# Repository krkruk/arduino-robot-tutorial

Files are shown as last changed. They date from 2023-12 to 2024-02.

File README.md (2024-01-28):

# arduino-robot-tutorial

The following pages introduce you into a world of embedded programming in AVR-based
[Arduino platform](https://www.arduino.cc/).

This repository is organized into the following directories:

* [Tutorial - rendered page](https://krkruk.github.io/arduino-robot-tutorial/) or [`docs`](docs/README.md) if you prefer to read raw Markdown files. The core tutorial you need.
* `/docs/chapters/assets/code` and `mini-robot` - these directories contains all intermediate code samples as well as the final code that can be simply uploaded to your Arduino microcontroller given you follow all the suggestions presented in the tutorial
* `3d_models` - all necessary STL files (including Solid Edge Community editable versions) to print your own robot!

The tutorial assumes you are at least familiar with C-lang-like language. It is not meant
to teach anyone how to code in AVR/Arduino from scratch. It's more like a getting started
for anyone who has some experience at coding.

Remember, education is important. Consider signing up for a university course. I'm just
a random guy in the Internet ;). Don't trust in anything you read... The tutorial likely has some issues with it, sometimes it may be misleading etc. Common sense is your friend, Google (or any search engine) is your bestie.

## Disclaimer

All presented materials serve educational purposes only. Working with electricity
poses hazard to your health and life. If you decide to follow the tutorial,
you do it at your own risk. You can get destroy your electronic components (i.e., ESD - electrostatic discharge), get electrocuted, burn down your surroundings. You have been warned!

Similarly, 3D printing comes with it's own risks. My first cheap 3D printer caught fire twice...
You need some basic skills to operate FDM/FFF printer. Please refer to your printer user
manual. Remember, you do it at your risk!

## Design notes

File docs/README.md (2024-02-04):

# Tutorial overview

## Introduction

Have you ever dreamed of making your own electronic device? 
Do you think it's a difficult task and requires at least a PhD in electronics?
Well, we no longer live in *Stone Age* and there is no need to chisel transistors out of a silicon wafer. There are way better solutions on the market nowadays.

This tutorial presents an affordable way to your very first robotics. For ~€20-25 you can build your own robot that actually can fight! 

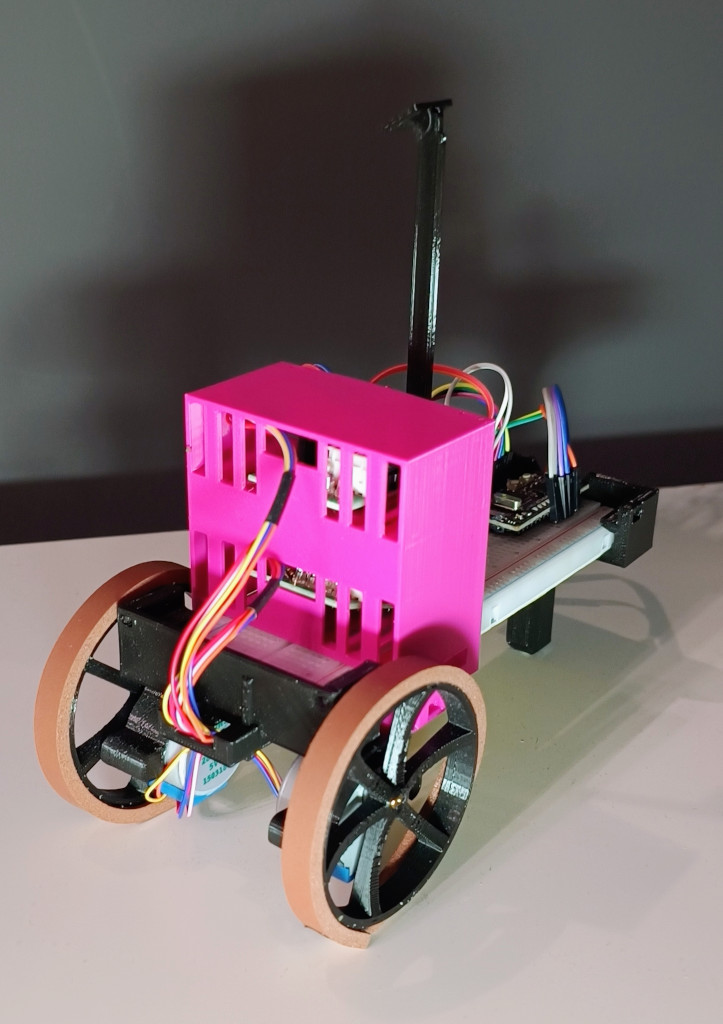
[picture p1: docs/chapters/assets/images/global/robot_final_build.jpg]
Robot - picture

<br />Figure: Completed robot, photo

> [!IMPORTANT]
> This tutorial assumes you have basic familiarity with one of C-like languages: C, C++, Java, JavaScript, Python.

This tutorial shall follow DRY principle: Don't Repeat Yourself. If there's a good resource, I'll simply point you there.

## Table of contents 
* [Hello World](chapters/0_hello_world.md)
  * Never seen an IDE? Want to test your set up? Come here!
* [I/O handling](chapters/1_io_handling.md)
  *  How to control pins in your board? Start here!
* [Analog input, Pulse Width Modulation](chapters/2_analog_and_pwm.md)
  * Life in between 0V and 5V
* [UART](chapters/3_uart.md)
  * Data transfer between PC and microcontroller
* [Controlling Stepper Motors](chapters/4_stepper_motor.md)
  * *You spin me right round round round...*
  * Full Step, Half Step, Arduino libraries
* [Controlling Servos](chapters/5_servo.md)
  * Torque and angle with a servo
* [Integrating knowledge - Building a robot!](chapters/6_robot_integration.md)
  * You are familiar with the basics by now. It's time to make a robot!

Your best friend during the course - [Atmega328P Datasheet](https://ww1.microchip.com/downloads/en/DeviceDoc/Atmel-7810-Automotive-Microcontrollers-ATmega328P_Datasheet.pdf)!

## Bill of materials

To complete the tutorial, you'll need:

* 1x justPi 830 breadboard (or other with compatible dimension)
* 1x Cytron Nano board (Arduino Nano board is a good choice too, though provides fewer features)
* 2x 28BYJ-48 stepper motors with ULN2003 driver (Darlington amp)
* 1x SG-92R servo (or similar)
* 1x set of jumper leads
* 1x set of resistors
* 1x set of LEDs
* 1x photoresistor 
* 1x microUSB cable
* 1x push button (optionally)
* 1x set of 3D printed elements (see below)

> [!NOTE]
> If you just want to learn basics you can complete the introductory chapters with only
> one stepper motor. You also don't need to 3d-print anything in that case!

## Bill of Materials: 3D printed elements
To complete the tutorial and build a robot, you'll need:

* 1x chassis_front_beam.stl 
* 1x chassis_rear_beam_with_airsoft_bearing.stl 
* 1x front_wall.stl  
* 1x rear_wall.stl 
* 2x stepper_motor_case.stl 
* 2x wheel.stl
* 1x driver_tower_with_servo.stl
* 1x servo_arm.stl
* 1x servo_arm_effector.stl
* 1x servo_holder.stl

Additionally:
* 1x plastic 6mm airsoft BB
  * That's your bearing and a part of the rear axle
* rubber strips to form a tyre (adhesive required). I used a window gasket/seal for this purpose. 
You can also cut a piece of a bicycle inner tube (so called *ranger band*). It fits perfectly and does
not require adhesives.
* Glue
* Some basic tools
* electrical tape
* a few zip ties can be quite handy too. Alternatively, you can use ancient technique of 
[cable lacing](https://en.wikipedia.org/wiki/Cable_lacing). After all, it's a formal NASA [NASA-STD-8739.4](https://s3vi.ndc.nasa.gov/ssri-kb/static/resources/nasa-std-8739.4a.pdf) standard.
Take a look at [NASA's website](https://workmanship.nasa.gov/lib/insp/2%20books/links/sections/401%20General%20Requirements.html).

All STL files can be downloaded from this tutorial repository: [3d_models](https://github.com/krkruk/arduino-robot-tutorial/tree/master/3d_models). 

The robot has been design to require no screws, bolts, anything. It's ugly but functional :).
Printing instruction:

* PLA is good enough. Some elements require precision of ~0.1mm 
* 6-10% fill
* 2 line wall thickness

Once you print all the parts, you'll have a robot that resembles the render photos below:

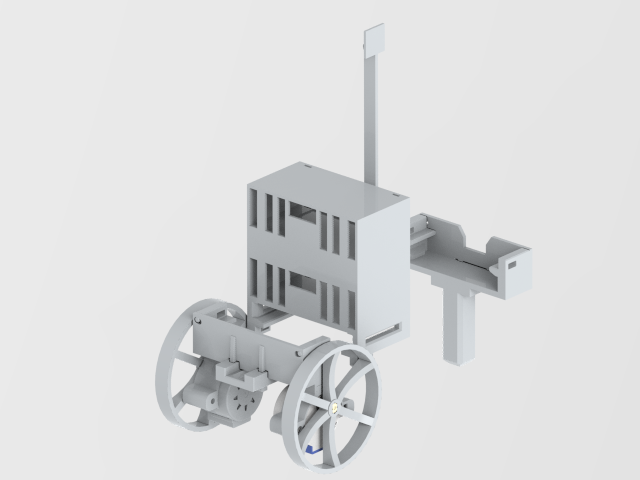
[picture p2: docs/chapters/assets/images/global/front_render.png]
Front render

<br />Figure: Front render

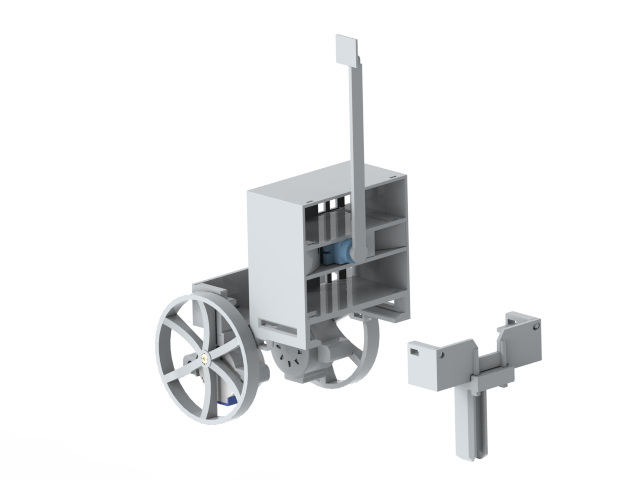
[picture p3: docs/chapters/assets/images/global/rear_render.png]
Rear render

<br />Figure: Rear render

## Integrated development environment

You need to install an integrated development environment to start developing your programs ASAP. It's the easiest and fastest way (of course you can use a standalone AVR Toolchain[^1] and AVRDude [^2]... it's your choice but make sure you have plenty of time and tenacity).

Since it's a quick way to get you started I suggest you install both, yes both, environments:

* VSCode/VSCodium + PlatformIO plugin. This is how you can do it: 
[Installation tutorial](https://docs.platformio.org/en/latest/integration/ide/vscode.html#ide-vscode)
* Arduino IDE - [download page here](https://www.arduino.cc/en/software)

Why two IDEs? Well, Arduino IDE is so simple that it's a very nice place to start. Lots of 
pre-installed examples that you can simply run. All toolchains install automatically (AVR, ARM, etc.). 
It provides an easy to use terminal to see UART data (refer to [UART](chapters/3_uart.md)). However, 
anything bigger than one file tends to be more and more difficult to maintain. 

VSCode is an advanced text editor that can work quite nicely as an IDE if you configure it properly. 
*PlatformIO* provides support for most of development boards available on the market. It also handles 
external dependencies quite well, so you don't need to download 3rd party libraries on your own. It 
all comes with a greater complexity and is slightly more difficult to use. Just slightly.

Now, sometimes it's easier to compile software in Arduino IDE than in VSCode. You download a lib, 
compile, and run. VSCode can sometimes be a pain in this aspect. So Arduino IDE is also a good tool 
for any quick debugging you may need.

## TL;DR; Skip tutorial, give me a robot

If you are impatient and want the robot now without following the tutorial,
here are all the steps you need to create your robot.

* 3d-print all elements you find in [`3d_models`](https://github.com/krkruk/arduino-robot-tutorial/tree/master/3d_models) directory. Use \*.stl files. Then, follow the assemble instructions
as provided in [Integrating knowledge - Building a robot!](chapters/6_robot_integration.md) chapter.
  in your favorite slicer software
* Follow the pinout as shown in the table
* Install the software on your Cytron board. Use README file distributed alongside
  the source code. Final code can be found [here](https://github.com/krkruk/arduino-robot-tutorial/tree/master/mini-robot/final_source_code).

**PINOUT**

| Device | Arduino Pin |
| --- | --- |
| Servo PWM line | D9 |
| Right Stepper IN1 | D7 |
| Right Stepper IN2 | D6 |
| Right Stepper IN3 | D5 |
| Right Stepper IN4 | D4 |
| Left Stepper IN1  | PIN_A4 |
| Left Stepper IN2  | PIN_A3 |
| Left Stepper IN3  | PIN_A2 |
| Left Stepper IN4  | PIN_A1 |

## Disclaimer

All presented materials serve educational purposes only. Working with electricity
poses hazard to your health and life. If you decide to follow the tutorial,
you do it at your own risk. You can get destroy your electronic components (i.e., ESD - electrostatic discharge), get electrocuted, burn down your surroundings. You have been warned!

Similarly, 3D printing comes with it's own risks. My first cheap 3D printer caught fire twice...
You need some basic skills to operate FDM/FFF printer. Please refer to your printer user
manual. Remember, you do it at your risk!

### References

[^1]: [GCC AVR Toolchain](https://www.microchip.com/en-us/tools-resources/develop/microchip-studio/gcc-compilers)
[^2]: [AVRDude](https://github.com/avrdudes/avrdude)

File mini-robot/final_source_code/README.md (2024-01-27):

# Arduino Robot Tutorial - Final Source code
## dependencies

* ArduinoJson 7.0.2 by Benoit Balnchon
* AccelStepper 1.64 by Mike McCauley
* arduino-timer 3.0.1 by Michael Contreras
* Stepper 1.1.3 by Arduino

## pinout

| Device | Arduino Pin |
| --- | --- |
| Servo PWM line | D9 |
| Right Stepper IN1 | D7 |
| Right Stepper IN2 | D6 |
| Right Stepper IN3 | D5 |
| Right Stepper IN4 | D4 |
| Left Stepper IN1  | PIN_A4 |
| Left Stepper IN2  | PIN_A3 |
| Left Stepper IN3  | PIN_A2 |
| Left Stepper IN4  | PIN_A1 |

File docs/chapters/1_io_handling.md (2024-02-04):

# Input/Output handling

**Contents**
* toc
{:toc}
Hopefully, you own an Arduino Nano-compatible board, just like the Cytron's one
mentioned in the *Bill of materials* page:

[Cytron Maker Nano pinout](https://www.cytron.io/p-maker-nano-simplifying-arduino-for-projects)

> [!IMPORTANT] 
> I strongly encourage you to support the original Arduino Project and the idea behind it! 
> Arduino enables thousands of people to develop hardware by reducing the learning curve.
> I strongly encourage you to buy one yourself!

The project can be completed using a standard Arduino Nano board.
The Cytron's board adds new features such as LEDs in all GPIO, a programmable button, and a buzzer. 
It's a nice touch if you want to reduce wiring in your final project.

> [!NOTE] 
> The board uses CH340C as a UART-USB converter. It's may not be compatible with your 
> operating system out of the box. 
> In *Ubuntu 22.04.3 LTS*, you'll need to configure it by uninstalling a package from your 
> system (it disables braille display): `sudo apt remove brltty` [^1]. MS Windows may require similar steps.

The Cytron's board uses Atmega328P as it's main microcontroller in the TQFP package. 
Luckily, you don't need to follow PCB paths to determine which board pin correspond 
to which IC pin. The pinout diagram above does it perfectly for you! Still, if it happens 
one day you need create your own PCB, it's worth to know physical 
dimensions and properties of your microcontroller (i.e. packaging, 
[DIP package](https://en.wikipedia.org/wiki/Dual_in-line_package)
or some sort of [SMD](https://en.wikipedia.org/wiki/Surface-mount_technology) like TQFP). 
You also want make yourself familiar with the original datasheet: 
[Atmega328P Datasheet](https://ww1.microchip.com/downloads/en/DeviceDoc/Atmel-7810-Automotive-Microcontrollers-ATmega328P_Datasheet.pdf). 
The datasheet provides all necessary information you need to start coding your microcontroller 
and tech specs that you should follow.

## PORTs, PINs and power output

What is a port, then? Well, in a realm of microcontroller, a port is a module that 
captures a signal from the real word, encodes and sends it over a data bus to CPU
([Processor, Central Processing Unit](https://en.wikipedia.org/wiki/Processor_(computing))) 
and/or other microcontroller peripheral elements.
A pin is a physical connector (a lead) that one can, for instance, solder onto a PCB. 
Pins are the true interface that the IC uses to interact with the world.

Atmega328p has 3 ports (PORTB, PORTC, PORTD) with built-in pull-up resistors. The 
microcontroller can therefore support up to 23 input/output pins 
(PORTC exposes 7 pins, the rest supports 8 pins). To visualize the overall Atmega architecture,
please refer to the documentation (chapter: 2). The block diagram (extracted from the datasheet *Chapter 2.1 Block diagram*):

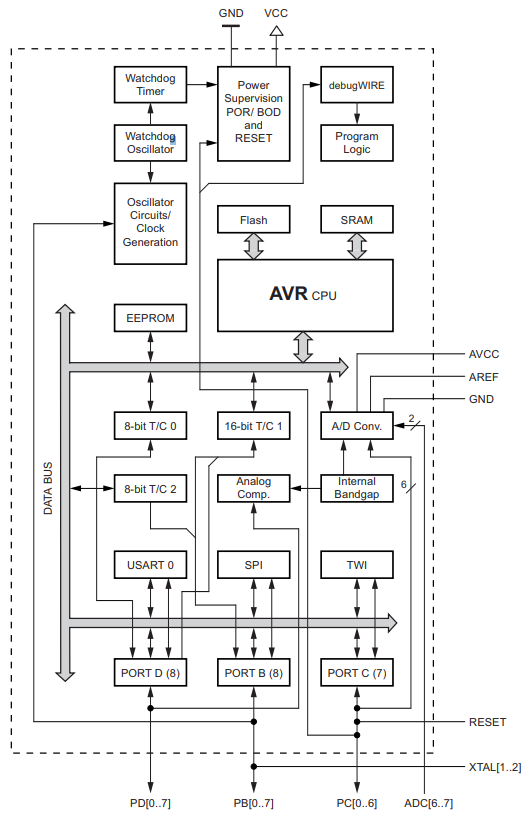
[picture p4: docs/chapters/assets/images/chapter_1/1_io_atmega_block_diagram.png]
Source: Atmega 328p datasheet, Chapter 2.1 Block diagram


That's a theory. You are not soldering your own PCB, you bought an off-the-shelf one. It means, 
you don't need to map pins defined in Atmega datasheet to your board outputs. Your Cytron's Nano is 
compatible with the original Arduino Nano, therefore you can re-use all resources known in 
Arduino to your advantage. Compare Cytron's pinout (the very first image in this page) with the 
table and the Arduino pinout below.

| PORT | Ardunio Nano | Cytron Maker Nano | Atmega328P |
|---|---|---|---|
| DDRB | D8 | D8 | PB0 |
| DDRB | D9 | D9 | PB1 |
| DDRB | D10 | D10 | PB2 |
| DDRB | D11 | D11 | PB3 |
| DDRB | D12 | D12 | PB4 |
| DDRB | D13 | D13 | PB5 |

[Arduino Nano Pinout](https://www.electronicshub.org/arduino-nano-pinout/)

`D\d` (for instance: `D8`, `D13`) is an alias for a given pin Arduino ecosystem. You don't need to
memorize anything. Your board has all the markings printed on the PCB solder mask itself. 
You will use the very same aliases such as `D8`, `D13` in your code if you decide to 
use Arduino framework. 
The Atmega328P pin aliases found in Atmega toolchain and are simply a shorthand for 
underlying pin addresses (i.e., `0x00`). You definitely want to use these aliases!
It improves overall readability and keeps your sanity intact anytime you decide to debug your code 
in future :).

If you want to know more about Nano board, you can refer to this page [^2].

## Digital output

> [!IMPORTANT] 
> Atmega328p pins are limited to 20mA (milli amps) per pin and up to 100/150mA for 
> a port. You should not connect anything more amp-consuming to a pin directly. Use a transistor 
> to amplify digital signals to an output that can handle bigger loads. You can read more on 
> amplifiers in [Wiki](https://en.wikipedia.org/wiki/Category:Single-stage_transistor_amplifiers). 
> Please, see also *28. Electrical Characteristics* in your Atmega datasheet [^3].

One more thing, Arduino Nano works in 5V logic. It means the high state (also referred as *1*) is 
5V and the low state is 0V (you guessed it! It's referred as *0*). That's the ideal condition, of course.
In the real world, *0* state can be considered as 1/3 VDD or lower of your voltage supply. 
Similarly, the high state is 2/3 VDD or higher [^4]. These are pretty good approximations.
You can also refer to *28.2 DC Characteristics* in datasheet for more details on 
input/out (high|low) voltages [^3].

Lots of theory, and no code so far. It's time to change it. Let's take a closer look to the 
blinking example we had in the previous chapter:

```
// Source: https://github.com/arduino/arduino-examples/blob/main/examples/01.Basics/Blink/Blink.ino

void setup() {
  // initialize digital pin LED_BUILTIN as an output.
  pinMode(LED_BUILTIN, OUTPUT);
}

// the loop function runs over and over again forever
void loop() {
  digitalWrite(LED_BUILTIN, HIGH);  // turn the LED on (HIGH is the voltage level)
  delay(1000);                      // wait for a second
  digitalWrite(LED_BUILTIN, LOW);   // turn the LED off by making the voltage LOW
  delay(1000);                      // wait for a second
}
```

The `setup()` function initializes hardware. It includes setting up a desired state on a pin,
interrupts, serial devices, etc.. Effectively, anything you need to run your main application code should be placed within the `loop()`.

The `loop()` function is effectively anything you want to run indefinitely as your firmware. 
This involves all ALU operations you want to run with help of your peripherals such as I/O pins, UART etc.

In order to blink an LED you always need to configure your port by telling a direction of a given pin, 
whether it's input or output. Possible options: `OUTPUT`, `INPUT`, `INPUT_PULLUP`.

Once this is done, you can then either write or read a pin state, depending on your direction 
configuration. To do so, you can use `digitalWrite(<<pin alias>>, <<state>>)` function. 
*Pin alias* can be a `uint8_t` value or a label such as `LED_BUILTIN`. *State* can be 
either `LOW` or `HIGH`.

Let's connect your own LED... You need an LED and a resistor. You should never connect an LED to a DC output as you will likely fry it. 

Basic LED circuit

First of all, if you have some experience in electronics you must know that LED is directional.
It means it acts as conductor if connected with correct polarity. If you connect it the other way 
around it won't conduct (well... until it does, briefly :)). The term is reverse current and it 
can be a feature sometimes. As this no 101 tutorial in electrical components, 
I suggest to take a look at Wiki [^5]. If you are in rush, I recommend taking a look at 
[voltage-current chart](https://en.wikipedia.org/wiki/File:Forward_and_Reverse_Characteristics_for_diodes-en.svg)
to understand how different LEDs can be.

S<sub>1</sub> voltage supply is the Arduino. It gives you 5V. LED requires 0.7V and 0.2mA to
light up. Now, you need to calculate what resistor is needed. 
The formula uses [Ohm's Law](https://en.wikipedia.org/wiki/Ohm%27s_law) and some 
[principles on connecting circuits](https://en.wikipedia.org/wiki/Kirchhoff%27s_circuit_laws) 
in series. I transformed it so it corresponds to the circuit

$$ R_1 = \frac{S_1 - D_1}{I} = \frac{5V - 0.7V}{20 \cdot 10^{-3}A} = 215 \frac{V}{A} = 215\Omega $$

Isn't the physics of electrics amazing? Now, you need to pick a resistor that matches the 
calculations. If you apply lower resistance value, you may fry your LED. I suggest to pick 220Ohm
resistor or higher. It's all math and diagrams. How to connect it? Well, let's go back to 
the real world. An LED has two leads: a short one and a longer one. The longer one is the 
'<strong>+</strong>' (katode) and the shorter one is '<strong>-</strong>' (anode). 
You want to connect your polarities in series, ie: `V+ - +R- - +D- - -V`. 
A '-' in component is a plus for the other one. You can also take a look at Adafruit's tutorial 
for more details [^6]. Oh, and as an interesting fact - the 
[colors on your resistor](https://en.wikipedia.org/wiki/Electronic_color_code) packaging matter!.

Please, construct your circuit as proposed here. You can use your jumper cables if you want:
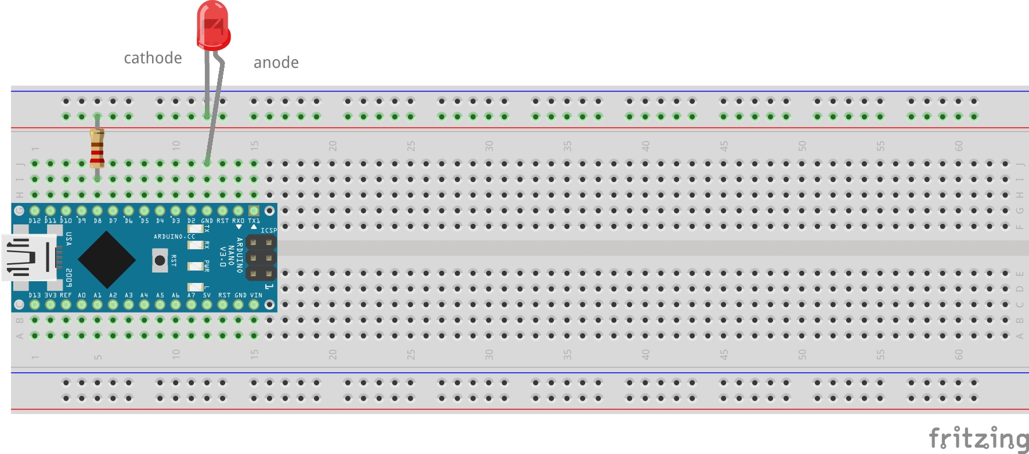
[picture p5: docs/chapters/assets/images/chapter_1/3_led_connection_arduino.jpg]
Arduino circuit

<br />Figure: Connecting an LED with a resistor

Now, the coding part! It's not that complicated
(source: [Incremental blink](./assets/code/chapter_1/1_incremental_blink/1_incremental_blink.ino)):

```
static constexpr const uint8_t HARDWARE_LED = 8;
static constexpr const uint8_t DELAY_RATE = 100;
static constexpr const uint16_t MAX_DELAY = 3000;

static uint8_t hardwareLedState = HIGH;
static uint8_t hardwareLedDelayCounter = 1;

void setup() {
  pinMode(HARDWARE_LED, OUTPUT);
  digitalWrite(HARDWARE_LED, HIGH); 
}

void loop() {
  uint16_t delayValue = DELAY_RATE * hardwareLedDelayCounter;
  ++hardwareLedDelayCounter;
  if (delayValue > MAX_DELAY) {
    delayValue = DELAY_RATE;
    hardwareLedDelayCounter = 1;
    hardwareLedState = HIGH;
  }

  hardwareLedState ^= 1;
  digitalWrite(HARDWARE_LED, hardwareLedState); 
  delay(delayValue);
}
```

The code increases delay time in each consecutive led state, i.e, 200ms - LOW, 
300ms - HIGH and so on. Note a new constant `HARDWARE_LED` - it matches `D8` pin in 
the Fritzing diagram above. If you use Cytron's board, you'll hear beeping sound too as `D8` pin
is connected to a buzzer

Ok, so how does it look like in pure AVR then. Well, in AVR context `setup()` and `loop()` functions
translate to this form:

```
int main() {
  setup();
  while(1) {
    loop();
  }
}
```

What Arduino Framework does is really it provides a layer of abstraction over the AVR microcontroller. 
It's way more developer friendly than dealing with raw registers. Speaking of registers, 
do you remember the blink example? This is pure AVR code 
(source: [AVR Blink](./assets/code/chapter_1/2_avr_blink/2_avr_blink.ino)):

```
#include <avr/io.h>
#include <avr/delay.h>

// This is the same hardware LED we introduced earlier!
#define HW_LED (1 << PB0)

int main() {

  /* setup() */
  DDRB = (1 << PB0);
  PORTB = (1 << PB0);  // light up the LED
  /* end: setup() */

  /* loop() */
  while (1) {
    PORTB ^= (1 << PB0);
    _delay_ms(1000);
  }
  /* end: loop() */
}
```

Isn't it way more complex, is it? Lots of bit shifts and poor readability. 
You certainly can see `setup()` and `loop()` blocks.

To initialize pin mode (remember: `pinMode()` function?), you need to follow documentation 
*13.2.3 Switching Between Input and Output* [^3] and set DDRB's value to 1, 
or precisely `0b0000 0001`. 
The port shall work as the output device allowing you to set/unset state. 
If you want to connect an LED to `D12` (also known as PB4), you can enable direction 
by assigning `DDRB = (1 << PB4)` or even `DDRB = 0b0001000`. 
To enable pin, you need to operate on a different register: `PORTB`. Operation `^=` means toggling a 
value under the given bit location. In Arduino, you would need to call 
`digitalWrite(pin, LOW|HIGH)` twice.

Clearly, AVR can be much harder to comprehend. So why bother? Well, some day you may be asked to 
implement a simple firmware on ATtiny13 (or similar), a microcontroller with very little resources. 
The AVR example requires 166 bytes, the Arduino one: 924bytes. Any framework shall add additional 
overhead and consume more flash disk space on your device. 
You need to be very conscious about resources and the platform limits 
(i.e., stack depth - nesting functions calls may also lead to errors!).

## Digital input and pull-up resistors
It's time to get some input events from the world. An obvious choice is a push button. 
A simple device that breaks a circuit if anyone pushes it...

Now, we already know that turning on an LED is to provide state **1**, which translates to 
5V potential at a pin. Good! How about we reverse the order. It'll be you who changes a potential 
on Arduino lead, which translates to a different state on a pin. All you need to do is to verify 
the state in the code!

Some theory is needed. You need to provide stable voltage on your pin. Otherwise, you can read 
any state state between 0 and 1, it'll float. This is why you need to construct a special circuit 
to support a button with a pullup resistor, such as this one:

Button circuit with pullup resistor

You are not limited to such a simple design. You can of course connect your button through a 
transitor, i.e., common collector circuit and/or a capacitor to the circuit to eliminate contact 
bounce [^7]. Eliminating contact bouncing can be done 
[programmatically](https://docs.arduino.cc/built-in-examples/digital/Debounce) but it's a rather tedious job to do.

More on pullup resistors can be found on Sparkfun's learning portal [^8] and debouncing here [^9].

Ok, that's all for now. It's a 3h tutorial after all. Let's do some coding. The Cytron board you 
have already has a push button! Let's use it! This is the button schematics (retrieved from 
Cytron's docs):

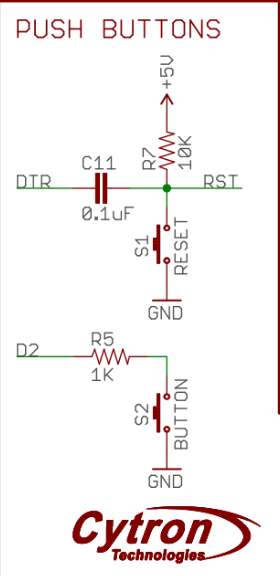
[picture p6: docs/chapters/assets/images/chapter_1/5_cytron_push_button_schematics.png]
Cytron Nano board - push button schematics
.

We are interested in the bottom part of the diagram. We can use programmatically `D2` pin. I hope 
you spotted that the button does not support physical debouncing, unfortunately. You can either 
code it on your own, based on the given resources or simply dismiss it. Here's a simple code 
snippet that changes an LED state anytime you press the button and keeps it until you push the 
button again (source - [3_pullup_and_software_debouncing](./assets/code/chapter_1/3_pullup_and_software_debouncing/3_pullup_and_software_debouncing.ino)):

```
static constexpr const uint8_t PUSH_BUTTON = 2;
static uint8_t builtinLedState = LOW;

void setup() {
  pinMode(LED_BUILTIN, OUTPUT);
  pinMode(PUSH_BUTTON, INPUT_PULLUP);
  digitalWrite(LED_BUILTIN, builtinLedState);
}

void loop() {
  uint8_t pushButtonState = digitalRead(PUSH_BUTTON);
  if (pushButtonState == LOW) {
    delay(50);                                    // simple programmatic debouncing
                                                  // You should measure the precise debouncing period
                                                  // with an oscilloscope. 50ms is just an educated guess
    pushButtonState = digitalRead(PUSH_BUTTON);

    if (pushButtonState == LOW) {
      builtinLedState ^= 1;                       // toggling the LED state
      digitalWrite(LED_BUILTIN, builtinLedState);

      while (digitalRead(PUSH_BUTTON) == LOW);    // blocking the program until
                                                  // the user releases the button
    }
  }
}
```

Interesting code parts: `pinMode(<<pin>>, INPUT_PULLUP|INPUT)`.
This is a pullup configuration for `D2 button`. From now on, you can read the state on 
the `D2` pin!. `digitalRead(<<pin>>)` function reads the state, either `HIGH` or `LOW`.

Another, *weird* part of the code is the nested if-statement and a delay function. Well, this is 
software debouncing. You push the button and connectors start to bounce back and forth. The 
program waits another 50ms until the connectors stabilize. The state should no longer float on 
that pin by the time the program reads the state again. If it is indeed low again, you change the
state of the button.

Note the last `while` loop at the end of the snippet. It blocks the application until 
the user releases the button. This is to prevent instant state toggling of the LED. 
Comment this out and see how your board behaves!

Now, how can you code the same thing in AVR? Let's see 
(source: [4_pullup_and_software_debouncing_avr](./assets/code/chapter_1/4_pullup_and_software_debouncing_avr/4_pullup_and_software_debouncing_avr.ino)):

```
#define LED_BUILTIN (1 << PB5)
#define PUSH_BUTTON (1 << PD2)

int main() {

  // setup()
  DDRB = LED_BUILTIN;
  DDRD = 0x00;          //set the enitre port as input - including PD2

  PORTB = 0x00;
  PORTD = PUSH_BUTTON;  //PD2 is set as input and the state as HIGH - pullup enabled

  // loop()
  while (true) {

    // the push button is pressed if it's state is 0

      if (bit_is_clear(PIND, PD2)) {  // much clearer than: !(PIND & (1<<PD2))
        _delay_ms(50);
        if (!(PIND & PUSH_BUTTON)) {
          PORTB ^= LED_BUILTIN;
          while (bit_is_clear(PIND, PD2));
        }
      }
  }
}
```

There are some major differences between this code and the Arduino one.
First of all, the state is kept in registers rather than in an application stack. 
There is also an additional register 
used: `PIND` (see docs: *13.4.10 PIND* [^3]). The register is responsible for reading the state 
on Atmega's lead. It returns all 8 bytes, each byte corresponds to one of the pins in your board. 
To read the state on PD2, you need to run some shifts to get data. Let's decipher this bit, 
assuming you actually keep holding the button:

```
values for:
  PIND = 0b???? ?0?? = 8 (? means state unknown)
  PD2 = 2
  1<<PD2 = 0b0000 0100 = 4

// button is pressed, state on the button lead is 0
1. !(PIND & (1<<PD2))
2. PIND & (1<<PD2)  --> 0b?????0?? & 0b00000100 = 0b00000000 = 0
3. !(0b00000000) = !(0) = !(false) = true  // zero is considered as false in C/C++/python
4. result: true

// button is released, state on the button lead is 1
  PIND = 0b???? ?1?? = 8 (? means state unknown)

1. !(PIND & (1<<PD2))
2. PIND & (1<<PD2)  --> 0b?????1?? & 0b00000100 = 0b00000100 = 8
3. !(0b00000100) = !(8) = !(true) = false // any non-zero number in C/C++/python is always considered as true
4. result: false
```

So really, all this complex math on bytes is all about reading a state on a given lead. If you
decide to use Arduino library, it's way easier to do so! Of course, it all comes with a price.
This is hex size for each framework:
* AVR hex size: 184 bytes
* Arduino hex size: 1086 bytes, more than 1kiB!

Good job! You know how to blink your LEDs both programmatically and with a push button. That's 
quite a lot. Really, interacting with a microcontroller is all about sending and receiving ones 
and zeros. All subsequent chapters only extend that notion! Can you imagine manually pushing and 
releasing a button 1000 times a second? This is what you will learn in the PWM chapter. Well, 
you'll learn how to do it programmatically, at least ;)

Let's move on to the next topic: interrupts. It's not the best idea to run blocking operations 
in the main program loop after all.

## Interrupts

Last but not least, we shall take a look at interrupts in this section. What is an interrupt? Well,
it's a mechanism that allows reacting to external (or internal) events outside of the main 
program loop? Wait, what? Let's take a look at an example, this time it'll be AVR code first 
(source - [5_interrupts_avr_toggle_led](./assets/code/chapter_1/5_interrupts_avr_toggle_led/5_interrupts_avr_toggle_led.ino)):

```
#include <avr/io.h>
#include <avr/interrupt.h>
#define LED_BUILTIN (1 << PB5)
#define PUSH_BUTTON (1 << PD2)

ISR(INT0_vect) {                   // magic here: Interrupt Service Routine
  PORTB ^= LED_BUILTIN;
}

static void setup() {
  DDRB = LED_BUILTIN;
  DDRD &= !(PUSH_BUTTON);          // pin as input
  PORTD = PUSH_BUTTON;             // pull-up

  EIMSK = 1 << INT0;               // enable PD2/INT0 as an interrupt source
  EICRA = 1 << ISC01;              // Enable direction of interrupt on INT0, 
                                   // falling edge
}

int main() {
  setup();
  sei();                           // enable global interrupts, SREG register

  while (true) {
    // idle, do nothing
    _delay_ms(10000);
  }
}
```

If you take a closer look at `while (true)` loop, you see it does nothing but sleeping. A good 
nap is nice but this is not why you bought your board to simply let it sleep... 
You want it to work for you and blink an LED!. If you compile it and start pressing 
the button you see that the LED turns on and off. Why? The interrupt!

There are some lines that can be somehow surprising. First of all `sei()` function. It enables 
global interrupts in `SREG` registry as documented in *6.3.1 SREG – AVR Status Register* [^3]. 
It's important not to forget to use it. In my personal experience, forgetting running this 
function is the most common reason why my interrupt routines don't work... it's because I don't 
enable them in the first place... There's also a function that has exactly opposite effect: 
`cli()` - it disables interrupts. It sometimes is handy as well.

Ok, interrupts are enabled. Now, we need to use PB5 (push button) pin as interrupt! 
Atmega328p offers two I/O pins as a source for external interrupts. 
Not much but still, we need to work with things we 
have\*. If you take a look at Arduino pinout from in the top of this page you'll notice that `PB5`
has also `INT0` label. That's the interrupt! Smartly design board, isn't it?

> \*you can set up interrupts as *PCIEx* that generates interrupts on many pins but it's out of 
scope of this tutorial

The setup functions sets up the `PB5` as a standard pullup-enabled input pin. There are two 
suspicious registers `EIMSK` and `EICRA`. `EIMSK` allows you to enable `INT0` as an interrupt 
source (vector) - see documentation *12.2.2 EIMSK – External Interrupt Mask Register* [^3]. The 
documentation states you need to set up an activation property to either raising or falling edge. 
You need the falling edge as you use a pullup-resistor. It means the high potential on the lead. 
So anytime you press the button, the potential goes to zero, hence the falling edge.
Of course, you can reverse that logic and use to your advantage. After all, it's all about
making engineering decisions.

Now, the most important part: `ISR()`. ISR is a special macro that handles interrupts in AVR. An 
*average* ISR body should be very concise and efficient. No long running operations as you block 
the main loop! Disabling interrupts and re-enabling them can be also a good idea if your code is 
highly asynchronous. You also should store `SREG` value to make sure you don't disable anything 
by mistake. ISR should then look more like this:

```
volatile uint8_t tmpSREG = 0;

ISR(INT0_vect) {                   // magic here: Interrupt Service Routine
  tmpSREG = SREG;
  cli();
  PORTB ^= LED_BUILTIN;
  SREG = tmpSREG;
}
```

Luckily, Atmega does this operation automatically, so you don't need to specify any `tmpSREG` 
variables [^10]. Hope, you noticed `volatile` keyword. Interrupts modify data outside of a 
regular program loop impacting the value that can be read from such a variable. The keyword 
prevents a compiler from optimizing the variable, improving stability of your application.

So what's an interrupt? A routine that reacts on an external/internal event and runs small 
portions of code called routines outside of a regular program loop. Hope, it's clear now. 
However, can you do the same thing in an easier way? Yes, you guessed it! Let's use Arduino this 
time! So here's the code that does the same thing, with no debouncing (source - 
[5_interrupts_avr_toggle_led](./assets/code/chapter_1/5_interrupts_avr_toggle_led/5_interrupts_avr_toggle_led.ino)):

```
static constexpr uint8_t PUSH_BUTTON = 2;
volatile uint8_t builtinLedState = LOW;

void toggleLed() {
  builtinLedState ^= 1;                       // toggling the LED state
  digitalWrite(LED_BUILTIN, builtinLedState);
}

void setup() {
  pinMode(LED_BUILTIN, OUTPUT);
  pinMode(PUSH_BUTTON, INPUT_PULLUP);
  digitalWrite(LED_BUILTIN, builtinLedState);
  attachInterrupt(                            // enabling interrupts on D2
    digitalPinToInterrupt(PUSH_BUTTON),       // mapping D2 to Atmega's INT0
                                              // this is for readability
    toggleLed,                                // a pointer to function, simply pass
                                              // a name of your function, it's not that scary!
    FALLING);                                 // activate the interrupt on falling edge
}

void loop() {
  delay(10000);
}
```

Hope, the resemblance is obvious... `toggleLed()` function simply performs a toggle operation on 
your built-in LED, using an external state variable. `enableInterrupt` well... enables the 
interrupt in nearly plain English. `digitalPinToInterrupt` maps a pin number to a corresponding 
event source pin, here `INT0`. This is certainly more readable and does not require much of 
knowledge on your board pinout. `toggleLed` here is simply passing a pointer to `toggleLed` 
function. You can use a more explicit way to show it's a pointer: `&toggleLed`, although I find 
it a bit of an overkill. Finally, you need to define a trigger that activates your interrupt. 
Choose FALLING trigger and keep in mind that there other options such as `LOW|CHANGE|RISING` [^11]. 

The `enableInterrupt` function works for digital pins only. Implementing a custom `ISR` can be 
more generic. Atmega328p support 26 input vectors as defined in 
`11.1 Interrupt Vectors in ATmega328P` [^3]. You can also browse `avr/iom328p.h` header to 
get the vector list:

```
[...]
/* Interrupt Vectors */
/* Interrupt Vector 0 is the reset vector. */

#define INT0_vect_num     1
#define INT0_vect         _VECTOR(1)   /* External Interrupt Request 0 */
// [...]
```

To summarize, the interrupts mechanism is a very handy tool if you want to support multiple 
actions in almost the same time. It allows you to act upon any external event 
and handle it efficiently.

Using interrupts and other Atmega peripherals allows you to implement a solution that appears to 
perform several actions in the same time. Multitasking, my friend :)!

## Analog input and output - ADC and PWM

Digital electronics, as your Atmega328p, is all about zeros and ones. 
There are no values in between, ideally. Thus, it's a rather hard task to talk about analog 
values in between 0-5V. Luckily, we are not exactly bound to 2 states only. We can change a pin 
state fast enough to reduce output power in a given timespan - this is called PWM, *Pulse
Width Modulation*. It's a rather important aspect of embedded programming, therefore
please read the next chapter that handles PWM in details.

There are also Arduino boards that support DAC - Digital-to-Analog converters, such
as [Arduino Due](https://store.arduino.cc/products/arduino-due). Unfortunately,
Atmega 328p microcontroller, as the one in your board, does not support DAC. For more details,
take a look at Wiki: 
[Digital-to-analog converter](https://en.wikipedia.org/wiki/Digital-to-analog_converter).

You can also read analog values with your microcontroller. Atmega328p comes with a 10-bit ADC and 
comparator built-in! ADC stands for Analog-Digital-Converter, which effectively translates voltage to 
a 10-bit value: 0-1023 integer value. More on ADC in the next chapter!

# References

[^1]: [CH340 Configuration in Ubuntu 22.04](https://askubuntu.com/questions/1403705/dev-ttyusb0-not-present-in-ubuntu-22-04)
[^2]: [Electronics Hub - Arduino Nano Pinout](https://www.electronicshub.org/arduino-nano-pinout/)
[^3]: [Atmega328P Datasheet](https://ww1.microchip.com/downloads/en/DeviceDoc/Atmel-7810-Automotive-Microcontrollers-ATmega328P_Datasheet.pdf)
[^4]: [Wiki - Logic Levels](https://en.wikipedia.org/wiki/Logic_level#Logic_voltage_levels)
[^5]: [Wiki - Diode](https://en.wikipedia.org/wiki/Diode)
[^6]: [Adafruit - Connecting LEDs](https://makecode.adafruit.com/learnsystem/pins-tutorial/devices/led-connections)
[^7]: [Wiki - Contact bounce](https://en.wikipedia.org/wiki/Switch#Contact_bounce)
[^8]: [Sparkfun - Pullup resistors](https://learn.sparkfun.com/tutorials/pull-up-resistors/all)
[^9]: [Physical Computing - Debouncing](https://makeabilitylab.github.io/physcomp/arduino/debouncing.html)
[^10]: [Stack Overflow - May I use cli() and sei() in the interrupt?](https://stackoverflow.com/questions/65112480/may-i-use-cli-and-sei-in-the-interrupt)
[^11]: [Arduino - attachInterrupt](https://www.arduino.cc/reference/en/language/functions/external-interrupts/attachinterrupt/)

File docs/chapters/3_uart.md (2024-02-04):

# Universal Asynchronous Receiver-Transmitter
**Contents**
* toc
{:toc}
So far, you've been blinking LEDs in one way or another. It's time to let your board talk to your PC too!.

See *19. USART0* chapter in Atmega328p Datasheet for very detailed UART tech specification [^1].

## Introduction

Serial port, [UART](https://en.wikipedia.org/wiki/Universal_asynchronous_receiver-transmitter) or 
[Universal Asynchronous Receiver-Transmitter](https://en.wikipedia.org/wiki/Universal_asynchronous_receiver-transmitter)
is a way that allows you to connect easily your device with PC and exchange data.

Asynchronous means that receiver/transmitter does not have to run at the same pace. Clocks of both 
devices can run at different frequencies or be out of phase. UART uses start and stop bits to 
determine when the transmission is over. This gives a great advantage. The protocol can work with no 
difficult clock synchronization techniques and technologies. 
Therefore, UART can be used at longer distances, speaking more of meters (yards) rather than 
centimeters (inches).

There are two industry wide standards of UART: [RS-232](https://en.wikipedia.org/wiki/RS-232) 
and [RS-485](https://en.wikipedia.org/wiki/RS-485). We are going to use a different route, though: TTL 
(Transistor-to-Transistor Logic) and connection via UART-USB bridge. In other words, you'll use Atmega 
integrated circuit, connect it to a 3rd party silicone chip (such as CH340, PL2303, FT232RL and many other) and plug a USB connector to your PC. You can even use another 
Atmega to host a USB (for instance Atmega16u4 with hardware USB support [^2])

Good news is your Arduino board (either Cytron's or the genuine one) comes with UART-USB converter. From coding perspective, you don't need to do anything.

A traditional UART tutorial presents and explains a data frame - a sequence of bits that form a single 
portion of a message... Let's get over with it now (image source: 
[Wiki - by Cody Hyman](https://pl.wikipedia.org/wiki/Plik:Serial_frame.png)):

UART data frame

Isn't it nice? Well, let me explain it from a perspective of typical parameters one typically uses:

* [baudrate](https://en.wikipedia.org/wiki/Baud) (popular: 9600, 115200) - originally, baud rate is a number of symbols/pulses emitted in a unit of time. In context of UART communication, think `baudrate=bitrate=bits per second` [^3]. Good enough, we are not purists here. And one more thing, the bigger the number, the faster is data transmission.
* dataframe (popular choice: 8 bits, 7-9 possible) - simply how many data bits shall be placed between the start bit and parity/end bits
* parity (set to no-parity) - a checksum bit, you can use it or simply ignore it. I prefer to ignore it. Other options are even and odd parity
* stop bits (popular choice: one; other options: one and a half, two bits)
* flow control (Arduino choice: No Flow Control) - UART supports two leads: RTS (Request to Send) and CTS (Clear to Send). Arduino uses TX and RX pins only, so there is no need to bother.

For a more detailed explanation, please refer to external sources such as this one: [UART - A hardware communication protocol](https://www.analog.com/en/analog-dialogue/articles/uart-a-hardware-communication-protocol.html) and other.

If you are going to connect your UART device to another device, make sure that:
* Baudrate must be the same for both a receiver and a transmitter
* Voltage levels are compatible: 5V-5V in both devices. Your device uses 5V as it's V<sub>cc</sub> voltage. If you connect to a device that uses 3.3V, you'll likely fry it. Hence, a [logic level converters/level shifter](https://en.wikipedia.org/wiki/Level_shifter) should be introduced.
* Cross your comm lines: `TX` (transmit line) should be connected to `RX` (receive line)
* NEVER FORGET ABOUT THE GROUND!!! GROUND IT!!! Actually, `GND` line should be the first line you connect and the first line you check if something is wrong. Seriously, you'll save lots of time by following this tip!

`TX1` pin is your transmitter and `RX0` is the receiver in your board. Take a look at it. Of course, you can simply use a USB cable if you plan to use PC comm only.

### Serial Monitors

You can use your serial device with a 3rd party tool or your custom software. If you decide to simply
browse or even plot data you can use some of these tools.

Windows:
  * [GUI] Arduino IDE - embedded serial monitor
  * [GUI] PlatformIO - embedded serial monitor
  * [GUI] [PuTTY](https://www.putty.org/)
  * [CLI] [Tabby](https://tabby.sh/)

Linux:
  * [GUI] Arduino IDE - embedded serial monitor
  * [GUI] PlatformIO - embedded serial monitor
  * [CLI] [minicom](https://en.wikipedia.org/wiki/Minicom)
  * [CLI] [Tabby](https://tabby.sh/)

If you are interested in writing your own software, you need a library or [follow a Lord's blessed path](https://en.wikipedia.org/wiki/TempleOS) and write your own library. It's up to you. Personally, I worked with the following:

* C++: 
  * Qt Framework, [Qt Serial Port](https://doc.qt.io/qt-6/qtserialport-index.html)
  * Boost Asio, [Serial Port](https://beta.boost.org/doc/libs/1_66_0/doc/html/boost_asio/reference/serial_port.html)
* python: [pyserial](https://pyserial.readthedocs.io/en/latest/pyserial.html)
* Java: [jSerialComm](https://fazecast.github.io/jSerialComm/)

## SerDes - Serialization and Deserialization

Data *serialization* is a process of converting data into a format that can be transmitted over 
wire/air and decoded at a destination point. The reverse process is called *deserialization*.

The keyword is **format**. You can choose two options: text or binary. The text option is usually 
human readable, supported by formats such as CSV, JSON, HTML, anything custom. The binary format 
converts data into a series of bytes, sometimes applying compression. You need to use the same 
serialization/deserialization technique in both receiver and transmitter to successfully deliver a 
message. Otherwise, the message can be consider as a series of random useless bytes.

Which one is better? Well, it depends. The binary format usually comes with big frameworks that can 
convert a *schema* into your C or C++ code. All you need to do is to compile a schema file and link 
generated files to your program. IMO, the greatest disadvantage of the binary format is difficulty to 
handle data packets. Since all your data is binary, you don't really know when the message stops and 
another message begins. A byte of binary data is really an 8-bit number, which translates to 0-255
(dec). Microcontroller is not aware of what the byte means. The binary formats of your choice usually 
provides libraries to capture a whole message and deserialize it, such as 
[protobuf](https://github.com/protocolbuffers/protobuf) or [msgpack](https://msgpack.org/), [ROS Messages](https://wiki.ros.org/Messages). 
Of course, you can implement something custom too - see the note below.

You can use text format too! It has several advantages: 1) it's human readable, 2) easy to find the 
last character, usually a new line character `\n`. Text format narrows down a range of values we send 
in a single byte from the binary data perspective. [ASCII](https://pl.wikipedia.org/wiki/ASCII) 
encodes human readable numbers as characters starting from a value 32 (in decimal, space `<<space>>`) 
up until 126 (dec, `~` character). Numbers between 0-31 and 127 
are special characters, such as *new line* character `\n` 10 (decimal). Thanks to this trick, a 
microcontroller can listen to a sender and cache raw bytes incoming from another UART device until it 
receives a byte of value 10 (dec, a new line character). You received a full line, a message that can be processed!

> [!NOTE]
> Long time ago, I was playing with robotics and European Rover Challenge. My team and I didn't know 
> anything about electronics and coding back then. We needed to control a robotic arm with 8 
> effectors. We developed a binary format -> one byte to control all 8 devices: `AAAV VVVV`. 
> `AAA` - 3 address bits, `VVVVV` - a value between 0-31. This technique allowed 
> us to control a 6-DOF arm without really any worries about a data package start and 
> stop positions. All we needed to do was to read just one byte to rule it all :)!

In my experience, hobby projects work very nicely with JSON (text) encoding. Simply, read a line of 
text data and deserialize JSON into individual variables. I recommend ArduinoJson[^4].

ArduinoJson deserialization example (source: [JsonParserExample](https://github.com/bblanchon/ArduinoJson/blob/7.x/examples/JsonParserExample/JsonParserExample.ino))

```
// ArduinoJson - https://arduinojson.org
// Copyright © 2014-2024, Benoit BLANCHON
// MIT License
//
// This example shows how to deserialize a JSON document with ArduinoJson.
//
// https://arduinojson.org/v7/example/parser/

#include <ArduinoJson.h>

void setup() {
  // Initialize serial port
  Serial.begin(9600);
  while (!Serial)
    continue;

  // Allocate the JSON document
  JsonDocument doc;

  // JSON input string.
  const char* json =
      "{\"sensor\":\"gps\",\"time\":1351824120,\"data\":[48.756080,2.302038]}";

  // Deserialize the JSON document
  DeserializationError error = deserializeJson(doc, json);

  // Test if parsing succeeds
  if (error) {
    Serial.print(F("deserializeJson() failed: "));
    Serial.println(error.f_str());
    return;
  }

  // Fetch the values
  //
  // Most of the time, you can rely on the implicit casts.
  // In other case, you can do doc["time"].as<long>();
  const char* sensor = doc["sensor"];
  long time = doc["time"];
  double latitude = doc["data"][0];
  double longitude = doc["data"][1];

  // Print the values
  Serial.println(sensor);
  Serial.println(time);
  Serial.println(latitude, 6);
  Serial.println(longitude, 6);
}

void loop() {
  // not used in this example
}
```

ArduinoJson will be used by default in subsequent chapters. Make sure to install it! Go to `Tools -> Manage Libraries...`, type `ArduinoJson` and click *Install*:

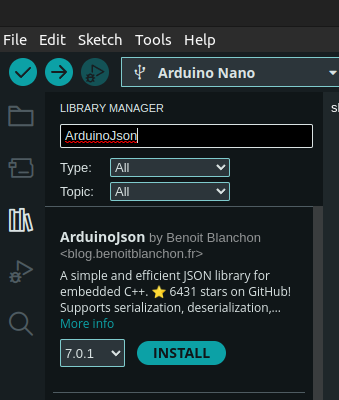
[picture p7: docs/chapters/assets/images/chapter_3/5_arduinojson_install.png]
ArduinoJson - Install steps


## Arduino Framework

Arduino allows using serial communication with ease. Make sure you familiarize yourself with documentation[^5].

### Serial initialization

This section shall present you how to write data to your PC. To connect with your microcontroller,
you can use Arduino Serial Monitor, PlatformIO Serial Monitor, minicom or really anything you
enjoy. The following examples shall use Ardunio Serial Monitor and minicom interchangeably.

Go to `Tools -> Serial Monitor`:

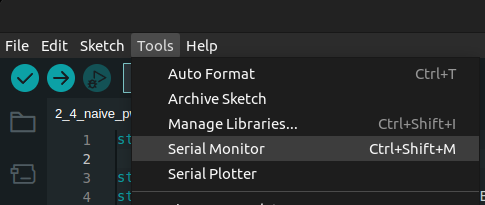
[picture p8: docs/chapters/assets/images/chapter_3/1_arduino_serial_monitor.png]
Arduino Serial Monitor


You'll see a new section at the bottom of your window. Make sure baudrate, newline setting and USB port are selected as shown in the picture (if you use Windows, port can be something like `COM7`):

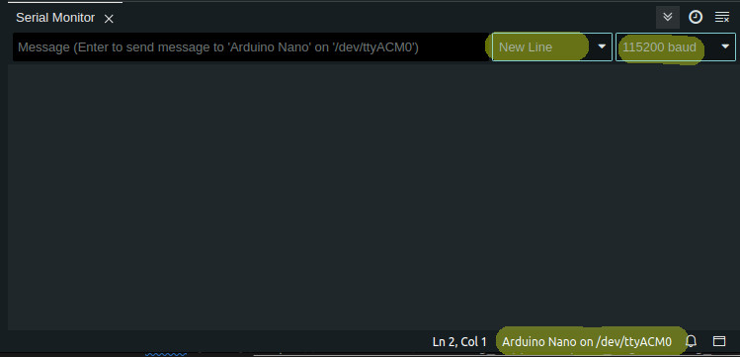
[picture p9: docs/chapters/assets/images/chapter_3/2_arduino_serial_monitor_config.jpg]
Arduino Serial Monitor - CLI


To start `minicom`, enter the following:

```
$ minicom -b 115200 -D /dev/ttyACM0
```

Minicom opens with `baudrate=115200`, 8-bits dataframe, 1 stop bit, no parity. Just like the Arduino Serial Monitor and the default Arduino Serial config (`SERIAL_8N1`)

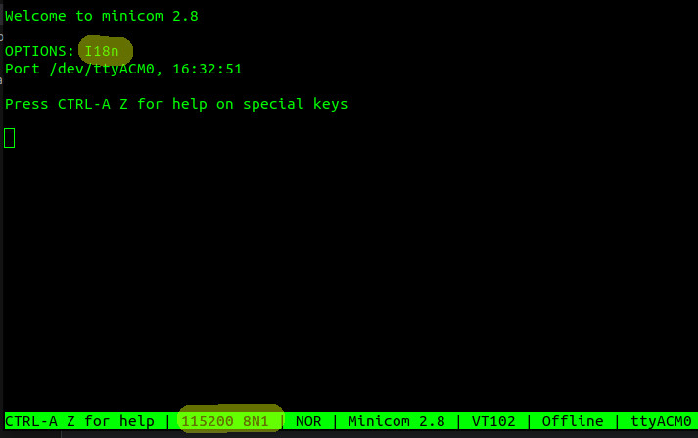
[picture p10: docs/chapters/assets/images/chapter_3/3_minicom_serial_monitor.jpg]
Minicom - Serial Monitor


You know how to open a serial monitor, now it's worth knowing how to start UART communication in Arduino.

There are two steps:

1. Initialize serial with baudrate and other config
1. Wait until a serial peripheral module starts (busy waiting)

Let's see some code (source - [Arduino Serial Initialize](./assets/code/chapter_3/arduino_serial_initialize/arduino_serial_initialize.ino)):

```
void setup() {
  Serial.begin(115200);
  while(!Serial) continue;
}

void loop() {
}
```

That's it! Isn't it simple? You probably have a feeling that these two lines hide some complex
register calls. That's correct! Let's now just focus on the positives: it takes two lines to enable Serial.

`Serial.begin(<<baudrate>>[, <<config, default: SERIAL_8N1>>])`[^6] initializes serial port to 
a given baudrate. Optionally, you can specify additional config for serial, should you need it. 
Otherwise, just enjoy simplicity of the API. Note that `Serial` is effectively a global variable 
that represents hardware serial. If you own an Arduino Mega, Due or any other that happened to support 
multiple UARTs, you can use other ports as well: `Serial1`, `Serial2`. You just need to make sure you 
connect necessary cables accordingly.

`while (!Serial) continue;` performs a busy waiting operation. The application waits here until the serial is initiated successfully. The implementation of `Serial` provides an overloaded `operator bool()`[^7]. 

Alright, we are ready to finally send some data to PC!

### Write data
#### Write a simple line

Without further edo, this is the code (source: [Arduino - UART Hello World](./assets/code/chapter_3/arduino_serial_hello_world/arduino_serial_hello_world.ino)):

```
void setup() {
  Serial.begin(115200);
  while(!Serial) continue;
}

void loop() {
  Serial.println("Hello World!");
  delay(1000);
}
```

To write a line, simply use `Serial.println()` function[^8]. It accepts raw strings 
such as `char *` and provides an overload for typical data types, such as `int`. 

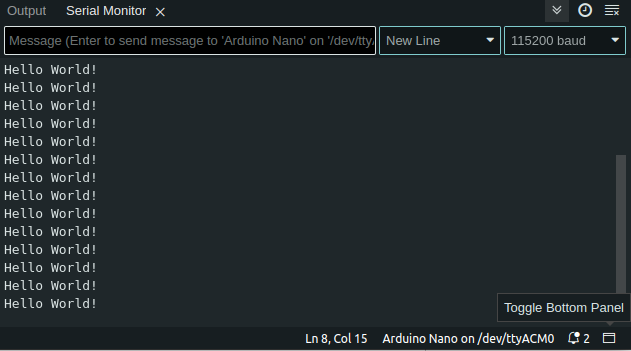
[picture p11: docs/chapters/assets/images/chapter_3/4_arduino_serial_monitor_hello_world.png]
Arduino Serial Monitor - Hello World


If you want to send an `int`, you can also
choose to print it either as decimal, octal or hexadecimal value, i.e.:

```
  Serial.println(15, DEC);
  Serial.println(15, BIN);
  Serial.println(15, OCT);
  Serial.println(15, HEX);

  result:
    15
    1111
    17
    F
```

Of course, there is also a function that does not add new line characters: `\r\n`. You can use [`Serial.print`](https://www.arduino.cc/reference/en/language/functions/communication/serial/print/).

Both `print()/println()` functions send data in a text format. Well, at least this is how data should
be interpreted at a receiving end. You can also send binary data with `Serial::write` function[^9]. As 
this course uses text-based serialization, I'll leave the binary part to study on your own. You can 
make it!

#### Write a line, substitute placeholders

Printing a static text is nice, but this is not how you use programs. You put data in and expect some results returned. How to send variable data? There are several options:
* Combine `print` and `println` into a sequence of calls
* Create a buffer string and generate a custom string
* Use a custom serializer: ArduinoJson or anything else
* Go with some sort of binary serialization and libraries

In this section, we'll try to go with the second approach (source - [Arduino - Buffer and sprintf](./assets/code/chapter_3/arduino_serial_buffer_sprintf/arduino_serial_buffer_sprintf.ino)):

```
#include <string.h>

static const constexpr uint8_t TXT_BUFFER_SIZE {64};
static char const TXT_BUFFER[TXT_BUFFER_SIZE] {'\0'};

static int counter {0};

static const char *HELLO_WORLD_LABELS[] = {
  "Hello World",
  "HELLO WORLD",
  "HeLlO WoRlD!"
};

void setup() {
  Serial.begin(115200);
  while(!Serial) continue;
  randomSeed(analogRead(0));
}

void loop() {
  uint16_t value = random(1000);                    // generate a random number
  char random_char = map(value, 0, 1000, 32, 127);  // random visible ASCII character
  ++counter;

  sprintf(TXT_BUFFER, "%s #%d: value=%d, char=%c",  // define a string and substitutions
    HELLO_WORLD_LABELS[counter%3],                  // substitute %s with a random string
    counter,                                        // substitute first %d with the counter
    value,                                          // substitute second %d with a random number
    random_char);                                   // substitute %c with a character

  Serial.println(TXT_BUFFER);
  delay(1000);
}
```

There are many things here. Let's dissect all of them. `TXT_BUFFER` is a static `char` 
buffer of size 64. `counter` and `HELLO_WORLD_LABELS` is just data that we want send dynamically. 
Similarly, `randomSeed(analogRead(0))` is a random number generator stuff... We want to send some 
dynamic data, don't we? This is it, random data generated on the fly.

Finally, we go to `loop()`. The first 3 lines is simply data generation. Finally, the application 
reaches `sprintf` function[^10]. It's a C-standard function here! Yes, you can use *some* of C and 
C++ libraries that come with AVR toolchain. `sprintf(<<buffer>>, <<format>>, <<args[]>>)`:
* `buffer` - it's a constant size buffer of characters. It's best to prefill it with `\0` characters
* `format` - it's effectively a string you want to analyze for any placeholders
* `args[]` - a list of values meant to substitute the placeholders found in `format`. Note that, AVR 
`sprintf` function DOES NOT support `float`/`double` data type!

Then, you simply write the buffer as your result with `Serial.println()` function. Effectively, all 
you need to do is to provide a buffer and come up with a `format` string. Pretty standard C!

#### Write JSON

You must install ArduinoJson first within your IDE. Please, address *SerDes - Serialization and
Deserialization* for more details.

The code roughly corresponds to the previous example (source: [Arduino Serial: ArduinoJson](./assets/code/chapter_3/arduino_serial_arduinojson/arduino_serial_arduinojson.ino)):

```
#include <ArduinoJson.h>
//ArduinoJson: 7.0.0

static int counter {0};
static const char *HELLO_WORLD_LABELS[] = {
  "Hello World",
  "HELLO WORLD",
  "HeLlO WoRlD!"
};

void setup() {
  Serial.begin(115200);
  while(!Serial) continue;
  randomSeed(analogRead(0));
}

void loop() {
  float value = random(1000) / 100.0;                    // generate a random number
  ++counter;

  JsonDocument doc;                                 // Dynamic memory allocation with malloc/free
  doc["str"] = HELLO_WORLD_LABELS[counter%3];       // Assign one of 3 strings dynamically
  doc["cntr"] = counter;                            // Assign cntr=counter
  doc["val"] = value;                               // Assign val=value
  //doc["r_char"] = random_char;                    // fail: must be converted to string

  serializeJson(doc, Serial);
  Serial.println();
  
  delay(1000);
}
```

Clearly, the data generation code is similar to the one presented in the previous section. This time,
`value` can be of `float` type! For use of `random()` function, please refer to the previous section
and Arduino documentation.

`JsonDocument` is the main library that help you serialize data into JSON object. Note, the library 
automatically detect variable type and uses corresponding serialization techniques. From your
perspective, it provides great comfort and ease of use!

Internally, `JsonDocument` uses dynamic allocators that can be somehow tricky to use. Generally, 
MISRA[^11] does not support dynamic heap allocations (`new/delete`, `malloc()/free`, etc.) 
in embedded programming. ArduinoJson in version 
*6.\** allows to statically allocate memory for that matter. In version *7.\**, you need to implement 
a custom allocator (github code: 
[ArduinoJson: Allocator](https://github.com/bblanchon/ArduinoJson/blob/7.x/src/ArduinoJson/Memory/Allocator.hpp)). 
You often want your code to be as deterministic as possible. This is to guarantee SLAs in certain 
use cases, i.e., aircrafts. This is one of the reasons why dynamic heap allocation can become 
a problem in huge apps.

Finally, all you need to do is to write a JSON object into Serial. You do it by calling 
`serializeJson(<<doc>>, <<Serial>>)`. Note, the API does not write it as a line, 
therefore you need to call `println().

Yes, that's all! Isn't it simple? Look at your results!

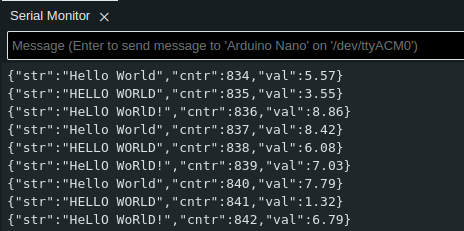
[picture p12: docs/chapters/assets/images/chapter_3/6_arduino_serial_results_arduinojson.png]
Arduino Serial - Arduino Json write


### Read data

You know how to write data, now it's time to implement a way to receive a command. Both examples deal
with turning on and off LEDs, most of them in your Cytron's board! 

#### Read a line of data

Note, this example uses Arduino's `String`[^12] that allocates memory dynamically. You can modify this example with `readBytesUntil` that accepts a static array of characters.

Code (source [Arduino - Read line](./assets/code/chapter_3/arduino_serial_read_line_as_string/)):

```
#include <math.h>

int pin = 0;
void setup() {

  DDRB = 0xff;        // all pins as output
  DDRC = 0xff;
  DDRD = 0xff;

  Serial.begin(115200);
  while(!Serial) continue;
}

void loop() {
  if (Serial.available() > 0) {
    String result = Serial.readStringUntil('\n');
    pin = result.toInt();                               // accept int only, 0 is an error value
  }
  
  if (pin != 0) {
    uint8_t pin_state = pin > 0 ? HIGH : LOW;
    digitalWrite(abs(pin), pin_state);
    Serial.print("PIN set to : ");
    Serial.println(pin, DEC);
  }
  pin = 0;
}
```

The program accepts integers, including negatives. For a negative value, the program turns off an LED. If is a positive one, an LED is turned on. The code enables all pins as OUTPUT (see `DDRB`, `DDRC`, and `DDRD` config). It's a rather greedy way to initialize but it works!

The core of the functionality happens in two lines:
```
  if (Serial.available() > 0) {
    String result = Serial.readStringUntil('\n');

    pin = result.toInt();                               // accept int only, 0 is an error value
```

First, the application verifies if UART input is active. If it is, the application can effectively 
wait until a full payload comes in. It's a blocking waiting function. No other steps shall be 
executed in the main loop of the program! Finally, [`readStringUntil()`](https://www.arduino.cc/reference/en/language/functions/communication/serial/readstringuntil/) returns with data.

By design, we know it's going to be an integer. Anything else shall result in an error value, exactly 
`0`. Remember about SerDes section? This is the moment where you introduce a contract between the 
microcontroller and a PC application you talk to. We decided to use an integer as an API. Nothing 
prevents you from applying something more complicated, as you'll see in the next section.

The application reads data until a new line character is received: `\n`. Windows uses `\r\n` as a new 
line delimiter. Still, it does not play a huge role in this example but it can be a possible issue
in your future project. Be aware of it!

By now, the application has all data it needs to run business logic! It turns on and off an LED
depending on a pin number you enter! It also sends a feedback back to Serial Monitor! Isn't it great!
Finally, your first useful app. Now imagine these LEDs are light bulbs, a kettle, a coffee machine and
so on. You can control them all with some basic knowledge on power electronics (i.e, how to use 
relays).

#### Read a line of JSON data

First, let's construct a JSON contract (schema). Let's say there are two options: LED_ON and LED_OFF. This is what your microcontroller is going to do after all. These are two possible values. JSON also 
needs a key. `op` should be good enough (short, yet descriptive). You want to keep your labels
rather short as you work on limited resources, RAM especially. You also need to specify a pin number.
Say `pin` key is good enough and a value is a positive integer.

You schema can look more or less like this:

```
{"op":"LED_ON|LED_OFF","pin":+int}

example:
  {"op":"LED_ON","pin":3}
  {"op":"LED_OFF","pin":3}
```

Now, let's take a look at the code (source - [Arduino Serial - Read serial as ArduinoJson](./assets/code/chapter_3/arduino_serial_read_as_arduino_json/arduino_serial_read_as_arduino_json.ino)):

```
#include <math.h>
#include <ArduinoJson.h>
#include <string.h>

enum class Operations {
  UNKNOWN_OP,
  ENABLE_PIN,
  DISABLE_PIN
};

void setup() {

  DDRB = 0xff;        // all pins as output
  DDRC = 0xff;
  DDRD = 0xff;

  Serial.begin(115200);
  while(!Serial) continue;
}

void loop() {
  JsonDocument doc;
  if (Serial.available() > 0) {
    auto error = deserializeJson(doc, Serial);
    if (!error) {
      uint8_t pin_state = LOW;
      const char *operation = doc["op"];
      Operations mode = strcmp(operation, "LED_ON") == 0
        ? Operations::ENABLE_PIN
        : strcmp(operation, "LED_OFF") == 0
          ? Operations::DISABLE_PIN
          : Operations::UNKNOWN_OP;

      int pin = doc["pin"];

      switch (mode) {
        case Operations::ENABLE_PIN:
          pin_state = HIGH;
          [[fallthrough]]
        case Operations::DISABLE_PIN:
          digitalWrite(pin, pin_state);
          Serial.print("Executed: ");
          serializeJson(doc, Serial);
          Serial.println();
          break;
        default: break;
      }
    }
  }
}
```

It looks way more complicated! Well, yes but not really. The code responsible for reading JSON is
this line `auto error = deserializeJson(doc, Serial);`. The rest is just applying business logic
to your code.

Line `const char *operation = doc["op"];` reads data under `op` key. The contract says, there are only
two acceptable options `LED_ON|LED_OFF`. There are lots of `strcmp` operations to convert it into
a value that can be accepted by the switch.

Line `int pin = doc["pin"];` is fairly simple. It reads a JSON value as int. There are no quote 
marks `""` in the JSON you send to the microcontroller `[...],"pin":3}`. This is core JSON 
specification.

The switch handles the operation, trying to be smart and limiting some code duplicates by 
implementing `[[fallthrough]]` label. It's meant to signalize that a missing `break` statement
is missing for purpose. In that way, the code automatically executes the next block of code.
Just a trick that saves some bytes in the microcontroller at cost of readability. You will need
to make such decisions if you are forced to fight for resources in any of your future projects!

The code eventually leads to the same overall functionality as the previous example. However,
thanks to JSON it can support additional features later in future! Simply adding a new key and 
adding a new business logic. It's not possible with the previous example in which you are forced to
rewrite deserialization part. It's even worse - you need to create your own standard and implement it.
It's time consuming and error prone.

With JSON you keep to one specification and all tools come included too. All you need to do is to
identify use cases. If you ever need extend functionality, you can add a new key/value with 
no impact on software that talks to your microcontroller.

Let's take a look at the results:

Arduino Serial - ArduinoJSON read, serial results

Observe your board. LED #3 performed an operation and returned a callback to Serial Monitor!

## UART, Atmega, Registers

You can apply principles you learned in the previous section and use it here, with raw Atmega
registers and implement all UART comms on your own! A few notes:

* USART details can be found in chapter *19. USART0*[^1]
* USART init code (*19.5 USART Initialization*), simple write (*19.6.1 Sending Frames with 5 to 8 Data Bit*) and read code (*19.7.1 Receiving Frames with 5 to 8 Data Bits*) snippets are provided in the documentation
* You can implement reading and writing as interrupt (`ISR(USART_RX_vect)` and `ISR(USART_TX_vect)`)
* USART reads and writes one byte at a time. You need implement caching mechanism yourself, i.e. [circular buffer](https://en.wikipedia.org/wiki/Circular_buffer)

In other words, low-level UART means lots of work. If you want to test your prototype quickly
it's pointless to reinvent the wheel. Simply, use a library such as Arduino Framework.

If you really want to take a look at UART/USART from a low level perspective, I suggest to read
the documentation first, then google term such `atmega328p uart example`.

Good luck!

## Other communication protocols

We are not limited to only one protocol. There are many others. I prepared a list of the most popular 
ones:

* [I2C](https://en.wikipedia.org/wiki/I%C2%B2C) also known as TWI (Two Wire Interface) in Atmega realm. You can read more in [I2C Arduino Tutorial](https://docs.arduino.cc/learn/communication/wire)
* [1-Wire](https://en.wikipedia.org/wiki/1-Wire). You can read more in [1-Wire Arduino tutorial](https://docs.arduino.cc/learn/communication/one-wire)
* [SPI](https://en.wikipedia.org/wiki/Serial_Peripheral_Interface). You can read more in [SPI Arduino tutorial](https://docs.arduino.cc/learn/communication/spi)
* [CAN](https://en.wikipedia.org/wiki/CAN_bus). You can read more about CAN here: [CAN protocol](https://embedclogic.com/can-protocol/), [Introduction to the Controller Area Network (CAN)](https://www.ti.com/lit/an/sloa101b/sloa101b.pdf?ts=1704879860080), [CAN Arduino Due library](https://www.arduino.cc/reference/en/libraries/due_can/). CAN is a standard comm protocol in automotive. Certainly, it's worth investing some time to know it better.
* SpaceWire :) - see ESA's [docs](https://www.esa.int/Enabling_Support/Space_Engineering_Technology/Onboard_Computers_and_Data_Handling/SpaceWire>)

# References

[^1]: [Atmega328P Datasheet](https://ww1.microchip.com/downloads/en/DeviceDoc/Atmel-7810-Automotive-Microcontrollers-ATmega328P_Datasheet.pdf)
[^2]: [Atmega16u4 Datasheet](https://ww1.microchip.com/downloads/en/devicedoc/atmel-7766-8-bit-avr-atmega16u4-32u4_datasheet.pdf)
[^3]: [What is the difference between baud rate and bit rate](https://stackoverflow.com/questions/20534417/what-is-the-difference-between-baud-rate-and-bit-rate)
[^4]: [ArduinoJson page](https://arduinojson.org/)
[^5]: [Arduino Serial - documentation](https://www.arduino.cc/reference/en/language/functions/communication/serial/)
[^6]: [Arduino Serial.begin()](https://www.arduino.cc/reference/en/language/functions/communication/serial/begin/)
[^7]: [Arduino Serial operator bool() overload](https://www.arduino.cc/reference/en/language/functions/communication/serial/ifserial/)
[^8]: [Arduino Serial - println](https://www.arduino.cc/reference/en/language/functions/communication/serial/println/)
[^9]: [Arduino Serial - write: binary data write](https://www.arduino.cc/reference/en/language/functions/communication/serial/write/)
[^10]: [CPP Reference - sprintf](https://en.cppreference.com/w/c/io/fprintf)
[^11]: [Wiki: MISRA C](https://en.wikipedia.org/wiki/MISRA_C)
[^12]: [Arduino String](https://www.arduino.cc/reference/en/language/variables/data-types/stringobject/)

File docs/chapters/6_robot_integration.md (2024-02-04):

# Robot integration
**Contents**
* toc
{:toc}
You've learned so much. Let's put that into practice and finally build your own robot!

## Introduction

Alright! You want to build a robot. This is the right place. I can simply provide you some steps
to achieve it. Still, this is not a purpose of this exercise. Let's think a bigger picture - engineering.

Normally, someone creates an item, a tangible object to fulfil a need. It can be a minor thing but
still its goal is to satisfy the need. Well? Why do we need to build a robot? 
It's fun, for sure. You also want to familiarize yourself with basics of microcontrollers and coding.
You did it in previous chapters. You are quite proficient at it! 
This chapter really integrates the knowledge. IMO, Building
a robot is the coolest way to do it. What sort of goals can we achieve with the robot? Are there any
alternatives? What's the context, etc.?

An engineer must ask a lot of questions to really understand the problem. After all, we try to solve
human problems rather than build cool stuff. (I know, here we intend to build cool stuff too. 
I generalize)

So what's our main mission? Say, you can bid a DARPA contract to win a robotic office battle. The
bid comes with a set of requirements you are expected to meet. Also the budget is limited, as DARPA
is willing to pay no more than €30 for a single robot. Specification can look like this:
* **DARPA/GENERAL/OFFICE-BATTLE/REQ/0010**: A device is a mobile platform, dimensions no greater than 20x20x10cm (length x width x height)
* **DARPA/GENERAL/OFFICE-BATTLE/REQ/0020**: The device shall be controlled over wire
* **DARPA/GENERAL/OFFICE-BATTLE/REQ/0030**: The device shall use commonly available off-the-shelf components
* **DARPA/GENERAL/OFFICE-BATTLE/REQ/0040**: The device shall compete non-destructively with other competitors to score points
* **DARPA/GENERAL/OFFICE-BATTLE/REQ/0050**: The device should not be equipped in any agent-dispersing equipment
    * (Consider this requirement as no flamethrowers, no chemical weapons, no shooting)
* and so on

The specification can of course be presented in different forms, formatting and so on (i.e., a few 
blocks of text...). Eventually, it's up to you to identify all possible requirements and assumptions 
to meet your client's needs. You can learn a bit more about it by reviewing some university competitions such as [Rules - European Rover Challenge](https://drive.google.com/file/d/1jZyn9oY7vqMJMvXQyE6EeLh7gRC0LpJh/view?usp=drive_link) or [Rules - University Rover Challenge](https://urc.marssociety.org/home/requirements-guidelines)

Note the language. Verbs such as is/shall/should/may/can/etc., one precise item mentioned in each 
bullet. The language of such requirements in the specification tries to be very detailed. 
In reality, even the most detailed description tends to be barely a draft once you attempt 
to implement it. There are simply too many factors to predict. 
Still, I wish you always get all the specs with no ambiguity.
Note the enumeration too. It's not always the case but usually it helps to navigate in documents
if you provide a decent convention. Imagine you need to talk to your client and discuss 
an unclear requirement. You can say that: on the 3rd page, 8th paragraph, second sentence the
requirement states that... and so on. Lots of words, too many actually. The enumeration helps
tracking this sort of problems in formal procurements as well as in future discussions.

The bid comes with a specification that defines a series of requirements. 
Now you need to model your further activities. What sort of actions the device, 
or from now on a robot, shall take? What
are the *rules of engagement*? Should the robot fight automatically? How to strike an opponent
within the given rules? How you can flex those rules, so it gives you market advantage :)?
There is lots of thinking involved... What are your skills (although it's not as important as it
can look like)? What's the budget? And so on...

The modelled design shall be presented in a form of a proposal. Yet again, there are many ways
to skin a cat... If it's a public institution, you might be given some clues, like [here (ESA)](https://www.esa.int/About_Us/Business_with_ESA/How_to_do/Preparing_a_technical_proposal)
or [here (NASA)](https://www.nasa.gov/wp-content/uploads/2022/02/2021_ed._nasa_guidebook_for_proposers.pdf).

Let me model that for you:
* **RB-GENERAL-REQ/0010**: The robot shall be a two wheel construction
* **RB-GENERAL-REQ/0020**: The robot shall be [controlled differentially](https://en.wikipedia.org/wiki/Differential_wheeled_robot)
* **RB-GENERAL-REQ/0030**: The robot shall be controlled at max distance of 1.5m from its control station (PC)
* etc.
* **RB-COMBAT-REQ/0010**: The robot shall engage at max distance of 12cm
* **RB-COMBAT-REQ/0020**: The robot shall shall strike an opponent by hitting it from top
* **RB-COMBAT-REQ/0030**: The robot shall shall perform at least 1 strike per second
* **RB-COMBAT-REQ/0040**: The robot may count received hits and announce opponent's score by
emitting a sound signal

These requirements shall convert into the following assumptions:
* **RB-GENERAL-IMPL/0010/REF:RB-GENERAL-REQ/0010**: The robot shall utilize 28BYJ-48 stepper motors to drive
* **RB-GENERAL-IMPL/0020/REF:RB-GENERAL-REQ/0010**: The robot shall be equipped with a set of wheels
 7-7.5cm in diameter, 3D-printed in PLA, rubberized tread
* **RB-GENERAL-IMPL/0030/REF:RB-GENERAL-REQ/0020**: The drive model shall be implemented within microcontroller
* **RB-GENERAL-IMPL/0031/REF:RB-GENERAL-REQ/0020**: The drive model shall comprise 4 commands: FORWARD, BACKWARD, TURN_LEFT, TURN_RIGHT. Turning shall be performed in-place. Power setting of min.0-max.255 shall be issued along with the drive command.
* **RB-GENERAL-IMPL/0040/REF:RB-GENERAL-REQ/0030**: The robot shall use microUSB cable and be supplied
with power output provided by USB3.0 (max. 900mA).
    * Comment: Energy budget is important! Each stepper consumes roughly 100-200mA @5V, servo in between 10mA-650mA[^1]. Arduino consumes 50-100mA. It means, the budget of 2x150mA + 300mA + 100mA ~= 700mA is under the total power output provided by USB3.0. We should be good here

* **RB-COMBAT-IMPL/0010/REF:RB-COMBAT-REQ/0010-0020**: The robot shall be equipped with a 12cm PLA-printed arm, driven by a servo mechanism
* **RB-COMBAT-IMPL/0020/REF:RB-COMBAT-REQ/0020-0030**: The combat arm shall be driven by SG-92R servo
* **RB-COMBAT-IMPL/0020/REF:RB-COMBAT-REQ/0040**: The robot should be equipped with a photoresistor
to count every opponent's successful strike

Note how precise this list is! IT IS INCOMPLETE! I didn't specified any programming languages nor
desired microcontrollers. It takes lots of work to complete the documentation. It takes even more
details to recreate a solution described in such a specification... I haven't even provided any 
drawings yet! Testing, maybe? Operational scenarios (a set of typical procedures to follow) and 
alternative scenarios ([FUBAR](https://en.wikipedia.org/wiki/List_of_military_slang_terms#FUBAR) cases).

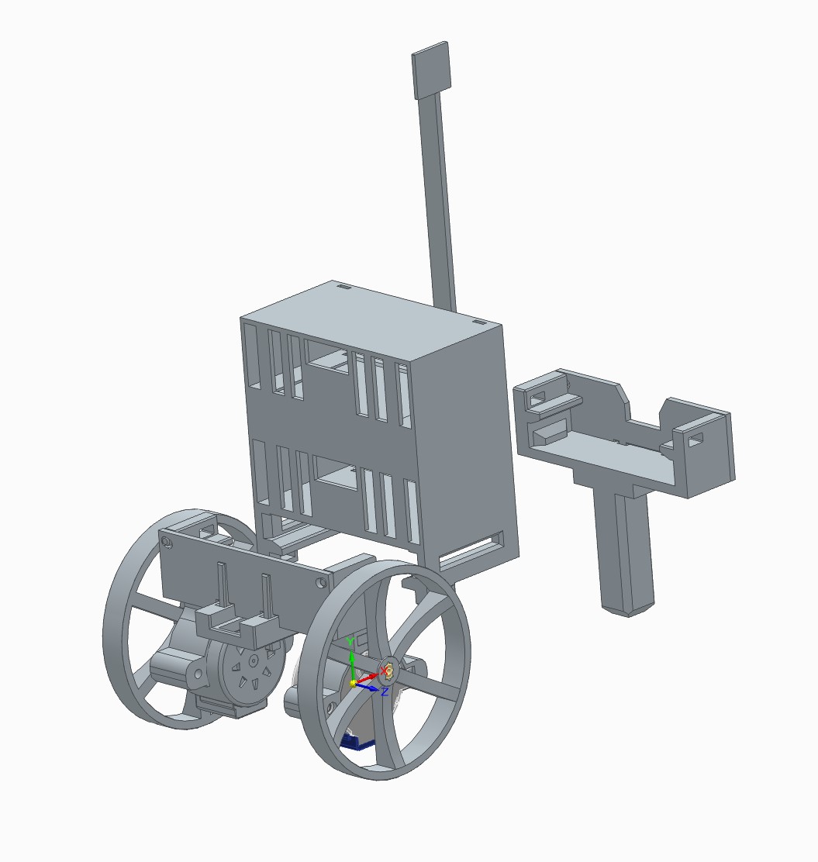
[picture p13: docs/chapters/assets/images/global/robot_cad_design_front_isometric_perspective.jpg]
Robot - isometric view front

<br />Figure: Robot, diagonal front isometric view

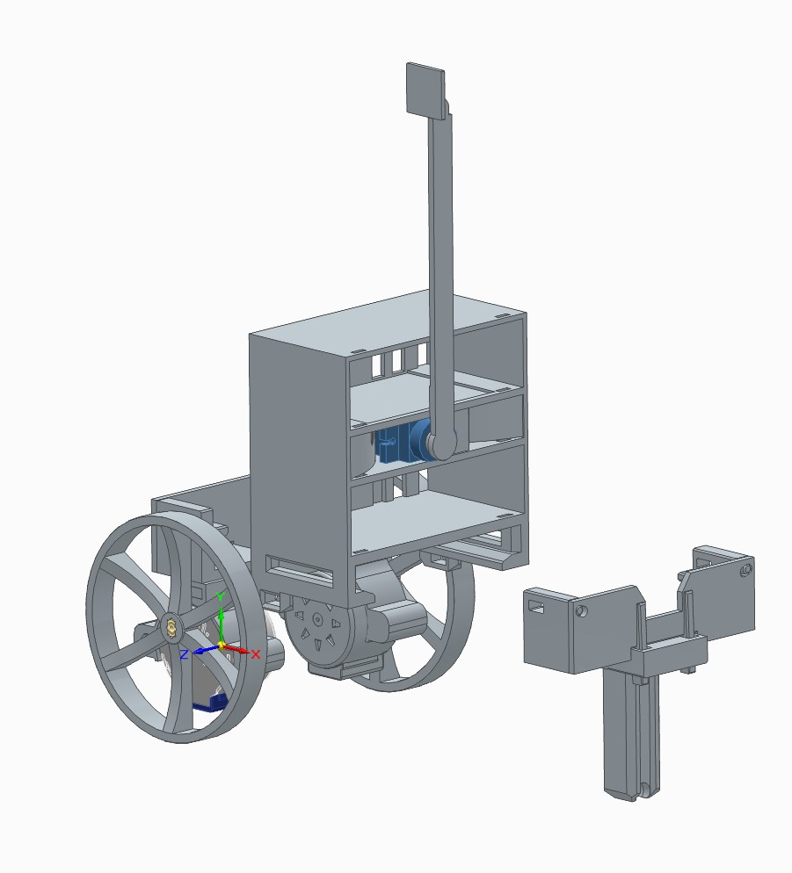
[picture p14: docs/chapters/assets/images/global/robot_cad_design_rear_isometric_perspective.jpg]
Robot - isometric view rear

<br />Figure: Robot, diagonal rear isometric view

Anyway, you should have now a general feeling over how the robot is going to look like: 2-wheels 
controlled with stepper motors and an arm that hits opponent robots from top.

This section was meant to introduce you to an engineering process that you may encounter in your
future work. Quite often, the documentation is the key to success. You can read more on project
management on [Wiki - Project Management](https://en.wikipedia.org/wiki/Project_management).

## Pinout

Make sure you follow the pinout as presented below:

| Device | Arduino Pin |
| --- | --- |
| Servo PWM line | D9 |
| Right Stepper IN1 | D7 |
| Right Stepper IN2 | D6 |
| Right Stepper IN3 | D5 |
| Right Stepper IN4 | D4 |
| Left Stepper IN1  | PIN_A4 |
| Left Stepper IN2  | PIN_A3 |
| Left Stepper IN3  | PIN_A2 |
| Left Stepper IN4  | PIN_A1 |

You can find the pinout in the code by the following references:
```
WeaponizedServo(uint8_t servoPin = 9, uint16_t deg0Micros=540, uint16_t deg180Micros=2540) 
const AccelStepper rightWheel; // default pinout:  (7, 5, 6, 4)
const AccelStepper leftWheel; //  default pinout: (PIN_A4, PIN_A2, PIN_A3, PIN_A1)
```

## Assembly

Make sure you printed all elements listed in Bill Of Materials!

Full assembly instructions:

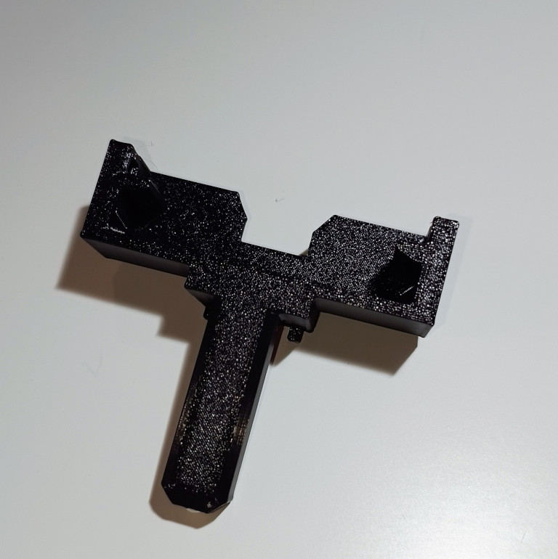
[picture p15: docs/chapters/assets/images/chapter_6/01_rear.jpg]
Rear - wall assembly

<br />Figure: Rear axle: Wall assembly

1) Assemble  `rear_wall.stl` with `chassis_rear_beam_with_airsoft_bearing.stl`. Mind the notches.
The support beams in `rear_wall.stl` should point outwards. See the next figures for more details

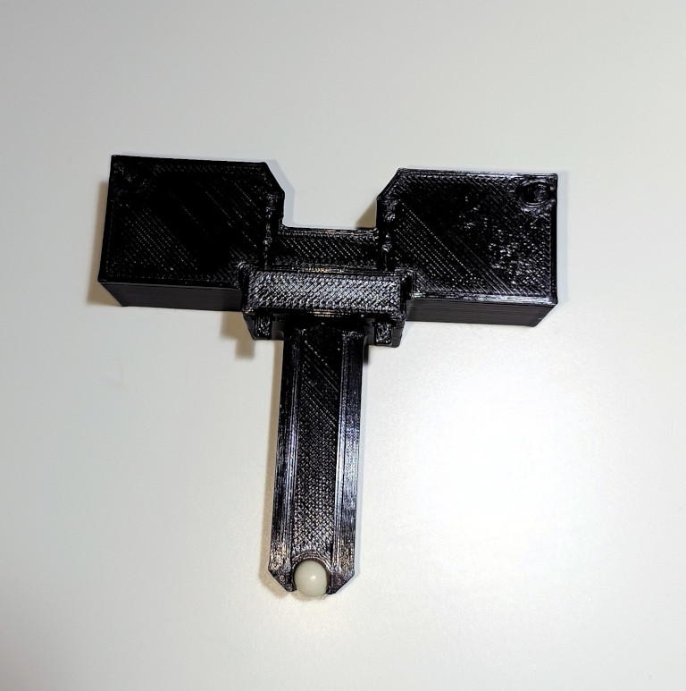
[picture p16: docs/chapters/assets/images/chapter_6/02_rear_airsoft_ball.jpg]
Rear - bearing assembly

<br />Figure: Rear axle: Bearing assembly

2) Insert a 6mm polymer ball into the notch in `chassis_rear_beam_with_airsoft_bearing.stl` at the
bottom

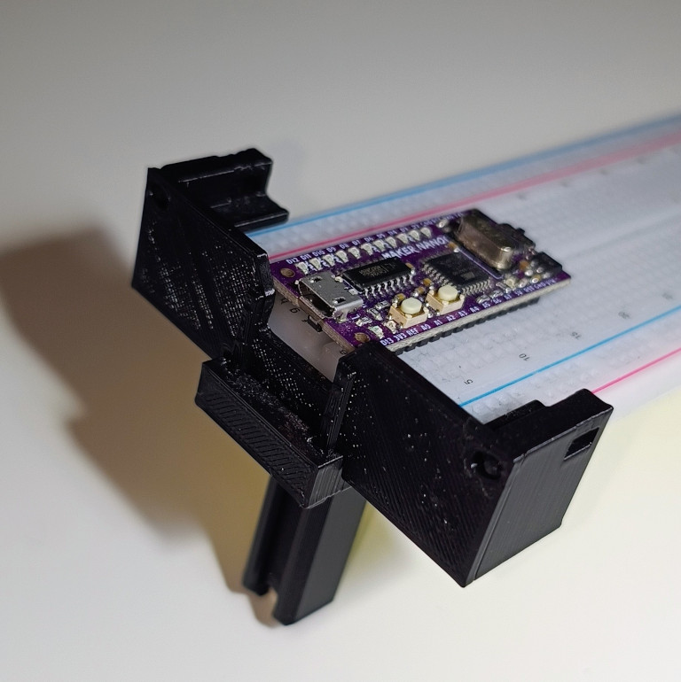
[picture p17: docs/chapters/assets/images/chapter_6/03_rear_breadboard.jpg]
Insert rear axle

<br />Figure: Install rear axle

3) Insert the breadboard into the axle as shown in the picture. This should fit tight. You can use 
a zip tie to tight the side walls: mind the openings in the sides: you can use it to insert a zip
tie

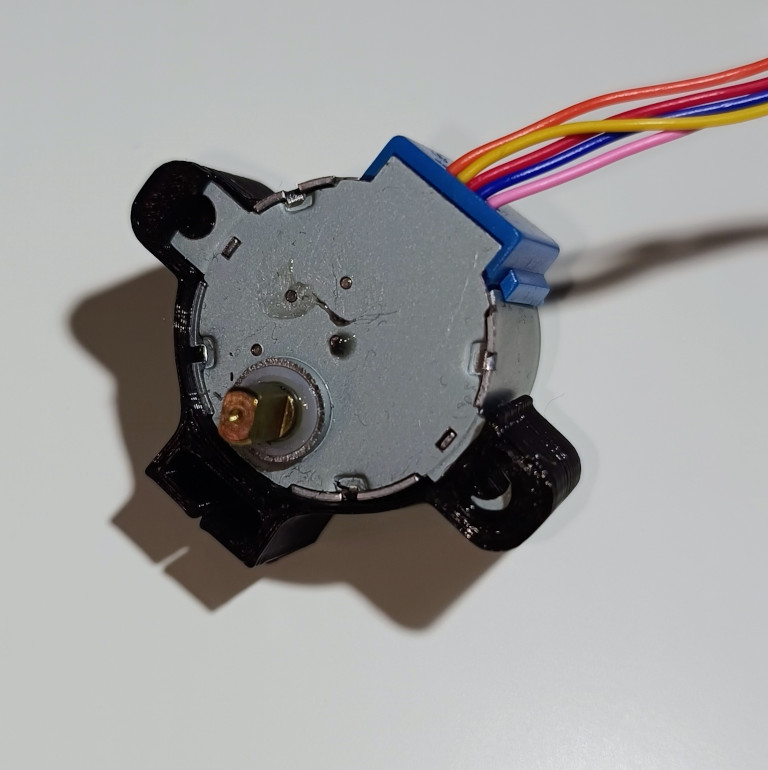
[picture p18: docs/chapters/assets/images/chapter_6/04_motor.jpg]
Motor assembly

<br />Figure: Motor assembly

4) Make sure you hold the stepper so the shaft is at the top. Insert the left piece 
into `stepper_motor_case.stl`. The print is elastic, you can bend it to accommodate for the necessary room. With a counterclockwise movement, insert the right piece of the stepper into the slot. Use some force as its very tight by design so no screw/bolts are needed. Perform this step twice

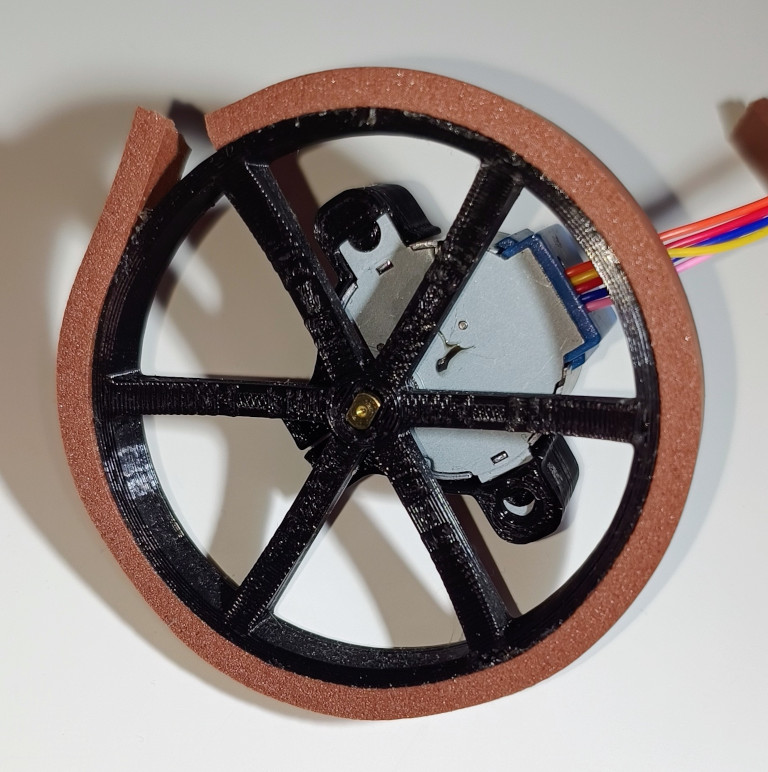
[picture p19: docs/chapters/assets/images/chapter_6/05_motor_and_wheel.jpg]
Wheel and stepper

<br />Figure: Install wheel

5) Glue a piece of rubber on top of the wheel. A typical window gasket/seal is good enough

6) Insert the stepper shaft into the slot. It is up to you to pick the wheel facing side

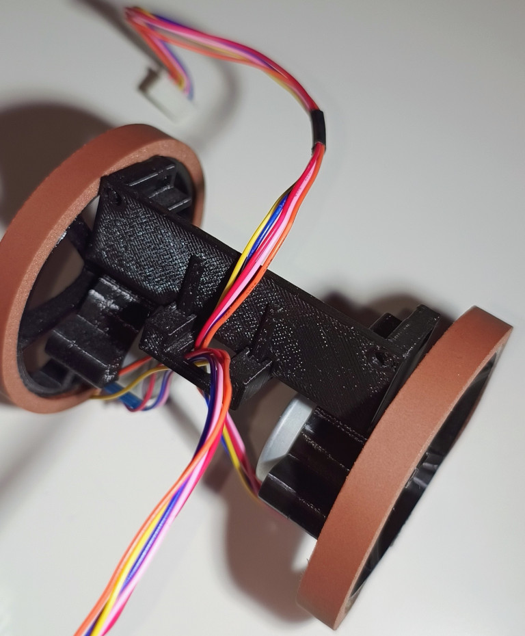
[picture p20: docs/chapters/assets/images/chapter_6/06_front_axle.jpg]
Front axle

<br /> Figure: Front axle assembly

7) Push each wheel onto `chassis_front_beam.stl`

8) Thread the stepper leads through the bottom opening

9) Install `front_wall.stl` with the support beams facing front. Mind the cables. You should
achieve the overall result as shown in the Figure

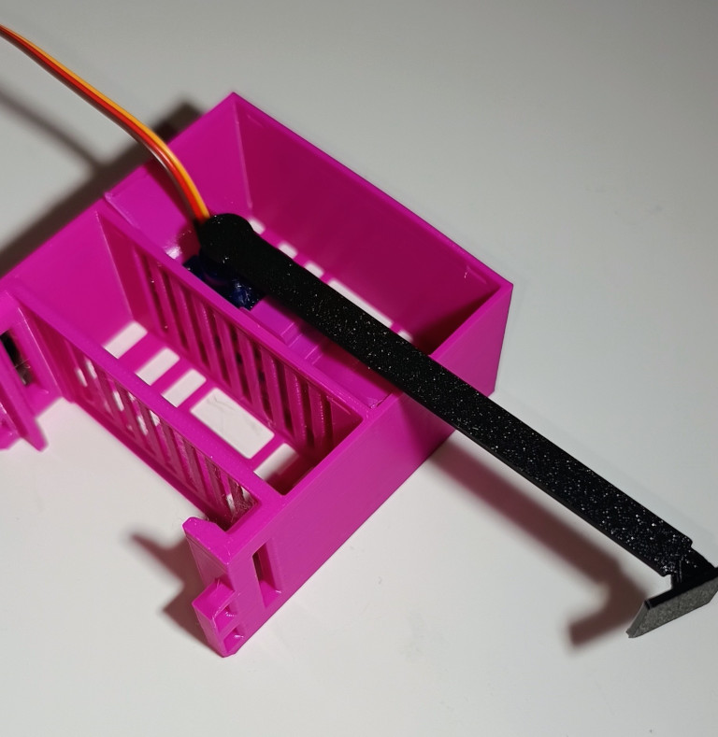
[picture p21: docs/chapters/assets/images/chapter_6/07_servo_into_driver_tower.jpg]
Install Servo

<br />Figure: Install Servo

10) Insert the servo into `servo_holder.stl`. There are two opening for the cabling. Make
sure you lay the cables through the openings

11) Insert the combined element into the middle drawer of `driver_tower_with_servo.stl`

12) Assemble the arm by gently installing `servo_arm_effector.stl` onto `servo_arm.stl`

13) Insert an asymmetric handle/needle/rudder into the assembled arm (no photos). The handle
comes with the servo in the same package

14) Push the assembled arm onto servo shaft. Do it gently as you need to calibrate the servo later.

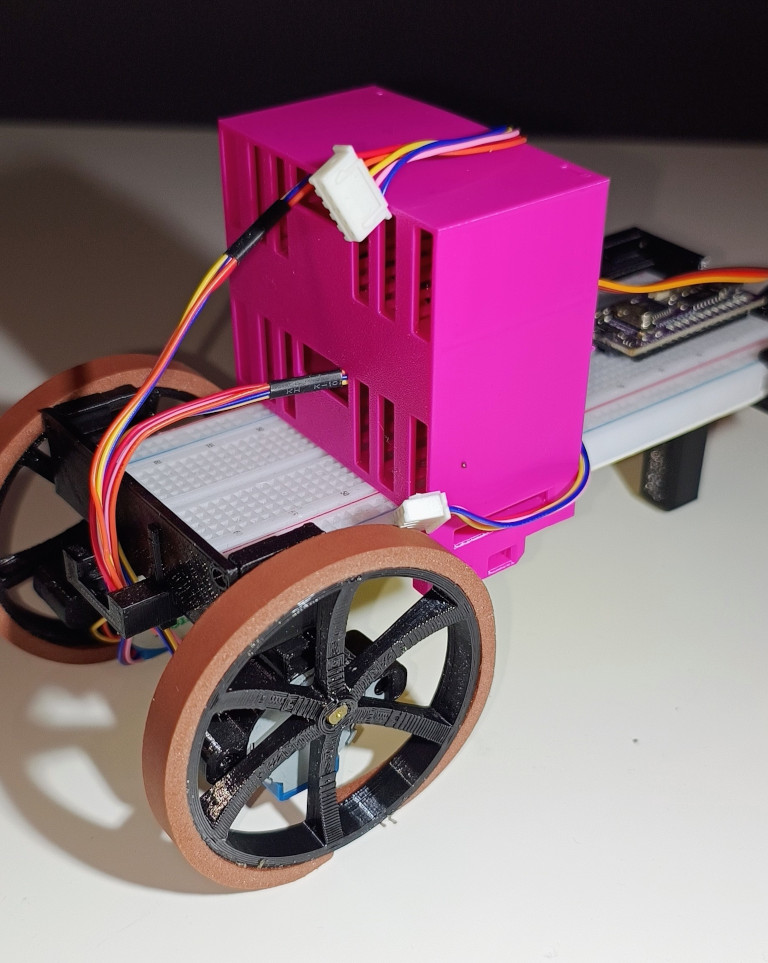
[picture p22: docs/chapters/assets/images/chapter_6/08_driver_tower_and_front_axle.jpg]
Front axle and driver tower

<br />Figure: Install front axle and the driver tower

15) Install the driver tower, so the small openings face forward

16) Install the front axle

17) Thread the stepper leads through the top and bottom notches. You should achieve the result 
as shown in the picture

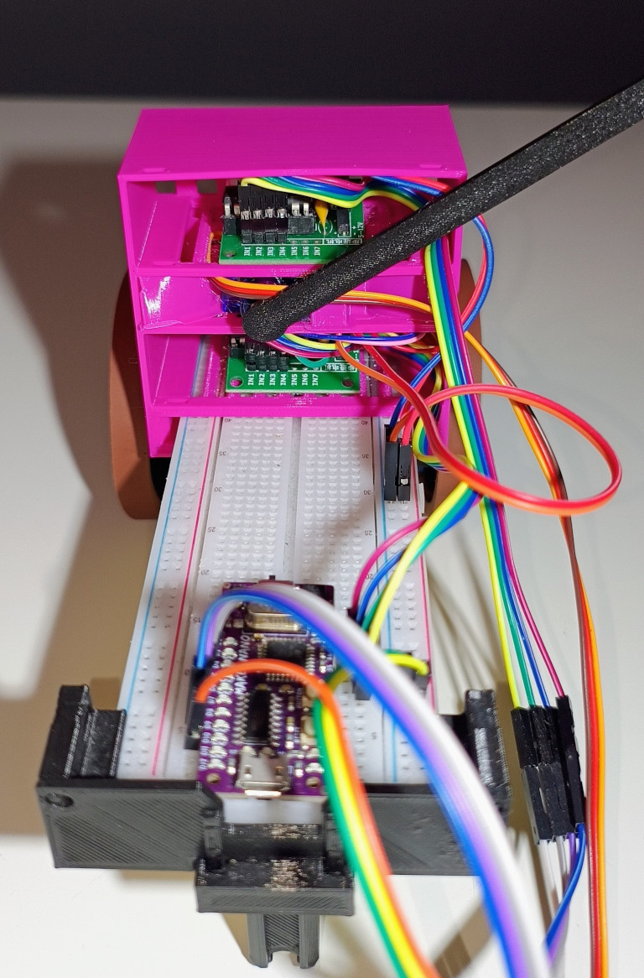
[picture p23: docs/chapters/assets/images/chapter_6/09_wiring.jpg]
Wiring

<br />Figure: Wiring

18) Connect all leads as suggested in the pinout table

19) Lay the cables in a way they have very low chances to interfere with the arm. Use zip ties,
thread, tape to order the cabling

20) We're done here. Move to the coding part :)!

## Coding

I chose more structural approach to write firmware for the robot. It's simply easier to
follow for unexperienced developers. If you familiar with C++ and OOP, you can develop
a hierarchy of classes if you want. Just allocate such objects on stack rather than heap.

### JSON contract

As explained in UART chapter, agreeing on a contract and data serialization is crucial.
In this section, we are going to define a set of commands to control the robot. The following
requirements and assumption provide some details of what's really expected:
* Drive: **RB-GENERAL-IMPL/0031/REF:RB-GENERAL-REQ/0020**
* Servo: **RB-COMBAT-IMPL/0020/REF:RB-COMBAT-REQ/0020-0030**, **RB-COMBAT-REQ/0020-0030**

Let's focus on the drive functionality. There are 4 expected actions:
* FORWARD (mnemonic: `FWD`): moves forward with a given power setting,
* BACKWARD (mnemonic: `BWD`): moves backward with a given power setting,
* TURN_LEFT (mnemonic: `T_L`): turns left with a given power setting, the turning starts only from
a stationary position
* TURN_RIGHT (mnemonic: `T_R`): turns right with a given power setting, the turning starts only from
a stationary position

Additionally, I want to add STOP command:
* STOP (mnemonic: `STOP`): wheels no longer spin, power cut-off, servo returns to its default position

Each mnemonic shall accept values in between: `0..255`. `STOP` mnemonic shall ignore the value but still, make sure to send zero, for API consistency.

You or a control app shall send only one of these mnemonics at the time.
Sample JSON:

```
{
    "FWD|BWD|T_L|T_R|STOP": 0..255
}

# example:
{
    "FWD": 128
}

# another example
{
    "STOP": 0
}

```

Servo definition can look like this:
* HIT (mnemonic `HIT`) - the servo performs a rapid strike and returns to its default position,
the code ignores any numerical value
* SERVO_POSITION (mnemonic: `SPOS`) - sets the servo into a position between 0..180 degrees. Allowed values: 0..180
* STOP (mnemonic: `STOP`) - places the servo to its neutral position

Similarly as in the drive case, you send either one of these two mnemonics:

```
{
    "HIT|SPOS|STOP": 0..180
}

# example (performs a hit):
{
    "HIT": 0
}
```

You can of course combine these commands and keep hitting an opponent while driving:

```
{
    "FWD": 255,
    "HIT": 0
}
```

You may be asking... why mnemonics? Well, microcontrollers have limited resources. Providing
long strings can severely impact on data processing or even cause memory issues. It's better
to keep it safely and use shorter names. Of course, I encourage you to experiment!

### Servo integration and calibration

See the [Controlling Servos](chapters/5_servo.md) chapter to calibrate the servo.

As the **RB-COMBAT-REQ/0020** assumption suggests, the arm should hit from top to bottom. This can be 
interpreted as keeping the arm in a vertical position. The hit would be *fast* move to a 
horizontal position. We can even overshoot a bit for the best *shock and awe* effect :D!.

Once you calibrate the servo, you should know the 0deg and 180deg positions. You can now adjust
the arm location at either of these positions and consider it as your default state. 
So say, the arm is vertical (or slightly tilted towards the hitting direction). 
Then, by applying 0deg or 180 deg position, the servo performs a hit. 
It's a question of how you inserted the servo into the driver tower box. 

This sample allows controlling servo in range 0..180degrees, as suggested by the JSON contract:

```
#include <Servo.h>

class WeaponizedServo {
  const uint8_t SERVO_PIN;
  Servo servo;
public:
  WeaponizedServo(uint8_t servoPin = 9) : SERVO_PIN{servoPin} {}

  void init() {
    servo.attach(SERVO_PIN);
    defaultPosition();
  }

  void changePosition(uint8_t angle) {
    angle = min(angle, 180);
    servo.write(angle);
  }

  void defaultPosition() {
    servo.write(45);
  } 
};

WeaponizedServo sledgehammer;

void setup() {
  sledgehammer.init();
}

void loop() {
  sledgehammer.changePosition(0);
  delay(1000);
  sledgehammer.changePosition(180);
  delay(1000);
}

```

See the `loop()` function. It's a temporary set of commands to simply test the servo. You want
to integrate one thing at a time so you minimize opportunities for errors. JSON integration will be
the last step in the process.

Ok, but what about the hitting mechanism? We need another method (function):

```
  void hit() {
    // servo is callibrated to 'hit' at 180deg angle
    servo.write(180);
    delay(350);
    defaultPosition();
  }
```

The problem about this function is it performs a blocking action in the main `loop()`. It means
that the robot shall stall for 350ms until it can drive again. That's suboptimal. We should
use something more non-blocking. You guessed it, an interrupt! The interrupt should be triggered
after 350ms to restore the servomechanism back to it's original position. The problem is
you need to precisely measure 350ms. We need a timer... Should be it a hardware one? It can,
but it's a rather tedious job to do... Let's use an off-the-shelf library, *Arduino-Timer*[^2].
Make sure you install it prior to running the code (source: [Servo Integration](./assets/code/chapter_6/01_servo_integration/01_servo_integration.ino)):

```
#include <Servo.h>
#include <arduino-timer.h>

class WeaponizedServo {
  const uint8_t SERVO_PIN;
  const uint16_t SERVO_0DEG_MICROS;
  const uint16_t SERVO_180DEG_MICROS;
  Servo servo;

protected:
  static Timer<2> timer;
public:
  WeaponizedServo(uint8_t servoPin = 9, uint16_t deg0Micros=540, uint16_t deg180Micros=2540) 
    : SERVO_PIN{servoPin},
      SERVO_0DEG_MICROS{deg0Micros},
      SERVO_180DEG_MICROS{deg180Micros} {}

  void init() {
    servo.attach(SERVO_PIN, SERVO_0DEG_MICROS, SERVO_180DEG_MICROS);
    defaultPosition();
  }

  void changePosition(uint8_t angle) {
    angle = min(angle, 180);
    servo.write(angle);
  }

  void defaultPosition() {
    servo.write(45);
  } 

  void hit() {
    // servo is callibrated to 'hit' at 180deg angle
    servo.write(180);
    WeaponizedServo::timer.in(350, [](void* thizz) -> bool { 
      static_cast<WeaponizedServo*>(thizz)->defaultPosition();
      return false; 
    }, this);
  }

  static void tick() {
    WeaponizedServo::timer.tick();
  }

  /*
  * Return true if the servo is ready to perform another hit.
  */
  operator bool() const {
    return WeaponizedServo::timer.empty();
  }

};
// initialize static timer
Timer<2> WeaponizedServo::timer;

WeaponizedServo sledgehammer;

void setup() {
  sledgehammer.init();
}

void loop() {
  if (sledgehammer) {
    delay(2000);
    sledgehammer.hit();
  }
  WeaponizedServo::tick();
}

```

As usual, there are many ways to skin a cat. I want to keep all servo-related actions
within the same class/namespace. Therefore I placed *Timer* within class and made it static
so you can also create an servo instance to support two hardware servos in total.

There is also `operator bool()` method that simply checks if there are any actions
pending. If there are no actions, then you can hit again :). Again, `loop()` contents
serves as a testing example. We'll provide the final code here at JSON integration step.

### Stepper integration

Servo is done, it's time for the stepper integration and make is a valid chassis. The
drive model is simplified. You can improve it later to let the robot turn while
driving forward. Arcs, and trigonometry - you're going to love it!

To make stepper work, I'm going to use *AccelStepper* library[^3]. Integration is fairly
straightforward. You just repeat steps found in *Stepper chapter* twice, for each servo.
Just be careful! The robot will try to run away!

The code (source: [Stepper Integration](./assets/code/chapter_6/02_stepper_integration/02_stepper_integration.ino)) implements 5 states in which a robot chassis can operate. See
the JSON contract proposed above. Code:

```
#include <AccelStepper.h>

class Chassis {
  const uint16_t MAX_SPEED;
  const AccelStepper rightWheel; // default pinout:  (7, 5, 6, 4)
  const AccelStepper leftWheel; //  default pinout: (PIN_A4, PIN_A2, PIN_A3, PIN_A1)

public:
  Chassis(uint16_t maxSpeed = 768,
    uint8_t rPin0= 7, uint8_t rPin1 = 5, uint8_t rPin2 = 6, uint8_t rPin3 = 4,
    uint8_t lPin0 = PIN_A4, uint8_t lPin1 = PIN_A2, uint8_t lPin2= PIN_A3, uint8_t lPin3 = PIN_A1)
    : MAX_SPEED(maxSpeed),
      rightWheel(AccelStepper::HALF4WIRE, rPin0, rPin1, rPin2, rPin3),
      leftWheel(AccelStepper::HALF4WIRE, lPin0, lPin1, lPin2, lPin3) {
        rightWheel.setMaxSpeed(MAX_SPEED);
        leftWheel.setMaxSpeed(MAX_SPEED);
  }

  void driveForwards(uint8_t speed) {
    auto stepperSpeed = 1 * mapSpeed(speed);
    rightWheel.setSpeed(stepperSpeed);
    leftWheel.setSpeed(stepperSpeed);
  }
  
  void driveBackwards(uint8_t speed) {
    auto stepperSpeed = -1 * mapSpeed(speed);;
    rightWheel.setSpeed(stepperSpeed);
    leftWheel.setSpeed(stepperSpeed);
  }

  void turnRight(uint8_t speed) {
    auto stepperSpeed = 1 * mapSpeed(speed);
    rightWheel.setSpeed(-stepperSpeed);
    leftWheel.setSpeed(stepperSpeed);
  }

  void turnLeft(uint8_t speed) {
    auto stepperSpeed = 1 * mapSpeed(speed);
    rightWheel.setSpeed(stepperSpeed);
    leftWheel.setSpeed(-stepperSpeed);
  }

  void stop() {
    rightWheel.setSpeed(0);
    leftWheel.setSpeed(0);
  }

  void run() {
    rightWheel.runSpeed();
    leftWheel.runSpeed();
  }

private:
  int16_t mapSpeed(uint8_t speed) const {
    return map(speed, 0, 255, 0, MAX_SPEED);
  }
};

Chassis chassis;

void setup() {
  // put your setup code here, to run once:
  chassis.driveForwards(200);
}

void loop() {
  chassis.run();
}

```

Private `mapSpeed()` function has been introduced to keep mapping logic in one place. If you recall
the assumptions, the allowed speed value is between 0..255, hence the mapping. Note also how 
`turnLeft()` and `turnRight()` functions are implemented. This is [differential drive](https://en.wikipedia.org/wiki/Differential_wheeled_robot) in which robot turns wheels in opposite
directions to cause rotation. This also explains why we need a BB ball as a bearing too :).

The code is straightforward and no further analysis is required. Please, refer to 
*Stepper motor* chapter if there is unclear.

### JSON Contract integration

By now, the robot can move and hit. It's time that the robot listens to our commands! Please,
refer to *JSON contract* section above if you find some decisions confusing. We have already
defined a set commands the robot should accept. It's time to just parse it and execute.

Code (source: [JSON integration](./assets/code/chapter_6/03_json_integration/03_json_integration.ino)):
```
#include <ArduinoJson.h>

JsonDocument json;

template<class K, class V>
class tuple {
  public:
  K key;
  V value;
  tuple(K key, V value) : key{key}, value{value} {}
};

class ChassisCommands{
  public:
  static constexpr const char * KEY_FORWARDS = "FWD";
  static constexpr const char * KEY_BACKWARDS = "BWD";
  static constexpr const char * KEY_TURN_LEFT = "T_L";
  static constexpr const char * KEY_TURN_RIGHT = "T_R";
  static constexpr const char * KEY_STOP = "STOP";

  enum ChassisCmdEnum {
    UNDEFINED,
    FORWARDS,
    BACKWARDS,
    TURN_LEFT,
    TURN_RIGHT,
    STOP
  };

  static tuple<ChassisCmdEnum, uint8_t> convert(const JsonDocument &doc) {
    if (doc.containsKey(KEY_FORWARDS)) {
      return tuple<ChassisCmdEnum, uint8_t>(FORWARDS, doc[KEY_FORWARDS].as<uint8_t>());
    } else if (doc.containsKey(KEY_BACKWARDS)) {
      return tuple<ChassisCmdEnum, uint8_t>(BACKWARDS, doc[KEY_BACKWARDS].as<uint8_t>());
    } else if (doc.containsKey(KEY_TURN_LEFT)) {
      return tuple<ChassisCmdEnum, uint8_t>(TURN_LEFT, doc[KEY_TURN_LEFT].as<uint8_t>());
    } else if (doc.containsKey(KEY_TURN_RIGHT)) {
      return tuple<ChassisCmdEnum, uint8_t>(TURN_RIGHT, doc[KEY_TURN_RIGHT].as<uint8_t>());
    } else if (doc.containsKey(KEY_STOP)) {
      return tuple<ChassisCmdEnum, uint8_t>(STOP, doc[KEY_STOP].as<uint8_t>());
    }
    return tuple<ChassisCmdEnum, uint8_t>(UNDEFINED, 0);
  }
};

class SledgehammerCommands{
  public:
  static constexpr const char * KEY_HIT = "HIT";
  static constexpr const char * KEY_SET_SERVO_POSITION = "SPOS";
  static constexpr const char * KEY_STOP = "STOP";

  enum SledgehammerCmdEnum {
    UNDEFINED,
    HIT,
    SET_SERVO_POSITION,
    STOP
  };

  static tuple<SledgehammerCmdEnum, uint8_t> convert(const JsonDocument &doc) {
    if (doc.containsKey(KEY_HIT)) {
      return tuple<SledgehammerCmdEnum, uint8_t>(HIT, 0);
    } else if (doc.containsKey(KEY_SET_SERVO_POSITION)) {
      return tuple<SledgehammerCmdEnum, uint8_t>(SET_SERVO_POSITION, doc[KEY_SET_SERVO_POSITION].as<uint8_t>());
    } else if (doc.containsKey(KEY_STOP)) {
      return tuple<SledgehammerCmdEnum, uint8_t>(STOP, doc[KEY_STOP].as<uint8_t>());
    }
    return tuple<SledgehammerCmdEnum, uint8_t>(UNDEFINED, 0);
  }
};

void applyChassisCommand(tuple<ChassisCommands::ChassisCmdEnum, uint8_t> cmd) {
  // do chassis thing
}

void applyServoCommand(tuple<SledgehammerCommands::SledgehammerCmdEnum, uint8_t> cmd) {
  // do servo thing
}

void setup() {
  Serial.begin(115200);
  while (!Serial);
}

void loop() {
  if (Serial.available()) {
    auto error = deserializeJson(json, Serial);
    if (!error) {
      auto chassisCmd = ChassisCommands::convert(json);
      auto servoCmd = SledgehammerCommands::convert(json);

      // business here 
      applyChassisCommand(chassisCmd);
      applyServoCommand(servoCmd);

      // prepare response
      json["chassisCmd"] = static_cast<int>(chassisCmd.key);
      json["servoCmd"] = static_cast<int>(servoCmd.key);
      serializeJson(json, Serial);      
      Serial.println();
      json.clear();
    }
  }
}
```

Quick explanation. `loop()` functions periodically reads data from Serial. `deserializeJson` is
a blocking, yet short, operations that awaits for a full JSON message. If you send a bulk message
rather than typing characters one by one, we should be fine with it.

The rest of the code is really handling the JSON. The critical part is parsing JSON keys to
use them as `enum`. Enum normally is a good way to tokenize a set of commands to anything you do.
`apply(Chassis|Servo)Command()` functions simply take an enum and a corresponding value and
apply to the business rules we defined earlier. I also introduced a helper class/object
to simplify coding: `tuple`. It provides a super-basic implementation of `std::pair`[^4]. Yet, it's
good enough for us. You can code 8-bit AVRs with modern C++11|17|20 but some standard libraries
are simply not available there.

### Combining all elements together!

Alright, it's time to combine everything together. The JSON integration part is the root of
the project. Simply copy and paste stepper and servo integration steps. We'll need to implement
two functions `applyChassisCommand()` and `applyServoCommand()`.

Let's see how these functions can look like (full source code: 
[Full integration](./assets/code/chapter_6/04_integrated_code/04_integrated_code.ino)):

```
// [...]
void applyChassisCommand(tuple<ChassisCommands::ChassisCmdEnum, uint8_t> cmd);
void applyServoCommand(tuple<SledgehammerCommands::SledgehammerCmdEnum, uint8_t> cmd);

static JsonDocument json;
static WeaponizedServo sledgehammer;
static Chassis chassis;

void setup() {
  Serial.begin(115200);
  while (!Serial);
  sledgehammer.init();
}

void loop() {
  if (Serial.available() > 0) {
  // cmd handling
  }

  chassis.run();
  WeaponizedServo::tick();
}
void applyChassisCommand(tuple<ChassisCommands::ChassisCmdEnum, uint8_t> cmd) {
  switch (cmd.key) {
    case ChassisCommands::FORWARDS:
      chassis.driveForwards(cmd.value);
      break;
    case ChassisCommands::BACKWARDS:
      chassis.driveBackwards(cmd.value);
      break;
    case ChassisCommands::TURN_LEFT:
      chassis.turnLeft(cmd.value);
      break;
    case ChassisCommands::TURN_RIGHT:
      chassis.turnRight(cmd.value);
      break;
    case ChassisCommands::STOP:
      chassis.stop();
      break;
    default:
      // unsupported operation
      [[fallthrough]];
  }
}

void applyServoCommand(tuple<SledgehammerCommands::SledgehammerCmdEnum, uint8_t> cmd) {
  switch (cmd.key) {
  case SledgehammerCommands::HIT:
    if (sledgehammer) {
      sledgehammer.hit();
    }
    break;
  case SledgehammerCommands::SET_SERVO_POSITION:
    sledgehammer.changePosition(cmd.value);
    break;
  case SledgehammerCommands::STOP:
    sledgehammer.defaultPosition();
    break;
  default:
    // unsupported operation
    [[fallthrough]];
  }
}
```

Hope you noticed two huge switches! This is one way to control commands in a microcontroller.
Switch is simple and easy to read. Another way is to create an array or a map of function
pointers. That would somehow easier to read but way more complicated from the language perspective.
AVR toolchains does not come with `std::function` to at least minimally simplify the implementation.
Hence, the switches. You can also use 
[*Command pattern*](https://refactoring.guru/design-patterns/command) too if you are familiar 
with OOP. Likely, you would implement it with some help of 
[CRTP C++ pattern](https://en.wikipedia.org/wiki/Curiously_recurring_template_pattern) 
to avoid polymorphic calls.

There is not much to talk about the code, really. Just read it carefully, you'll understand it perfectly. Some remarks, 
though:
* `static` JsonDocument, Chassis and WeaponizedServo - static here means to keep these
variables in a single compilation unit (think: file). If you decide to use it in different files, the 
objects won't work. It's a very C/C++-related thing. Just browse the keyword. `static` means many,
too many things in C++
* `setup()`, don't forget to initialize Serial and the servo!
* `loop()`, don't forget to run your `tick()` and `run()` methods. Otherwise, the steppers and the 
servo won't work!
* `if(sledgehammer)` this statement uses an overloaded bool operator. Simply, the logic
does not allow initiating a hit in the middle of the previous hit. You can of course play with it.
* `apply(Stepper|Servo)Command()` definition has been split into separate definitions and declarations.

The Arduino file is quite huge by now ~250 lines by now. It's worth to refactor it into separate
files. You can also see how heavy the firmware is:

```
Sketch uses 16582 bytes (53%) of program storage space. Maximum is 30720 bytes.
Global variables use 579 bytes (28%) of dynamic memory, leaving 1469 bytes for local variables. Maximum is 2048 bytes.
```

Remember previous chapters? Direct hardware access can heavily optimize resource usage. On the
other hand, it wouldn't be so easy to implement as the samples shown above.
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

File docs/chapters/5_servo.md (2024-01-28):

# Servo control
**Contents**
* toc
{:toc}
This chapter is all about servomechanisms, servos for short. You will learn: 
* What is a servo? How does it work?
* How to connect a servo?
* How to control a servo?
* Different types of servos

## Theory

A servomechanism (servo) is a feedback system that uses a closed-loop controller to set
and actively adjust its position and/or velocity as an actuator[^1], [^2]. There are many types of
servos i.e., hydraulic, pneumatic, electric [^1]. In this tutorial, we shall focus on typical
positional rotation DC motor servos, often used in RC control models.

Let's quickly decipher the definition to fit our context:
* servo does rotate
* servo does keep its position
* servo can be controller with a microcontroller

Internally, a servo is an effector (here: a DC motor) wrapped with electronics that read and 
control its position. To read a position you need some sort of 
[*encoder*](https://en.wikipedia.org/wiki/Encoder_(position)). You also need a control 
mechanism/circuitry to read the position and correct it.
Often, it's a microcontroller with custom software, usually a [PID controller](https://en.wikipedia.org/wiki/Proportional%E2%80%93integral%E2%80%93derivative_controller). 
Finally, the servo needs to actuate in the real world. 5V/20mA is barely enough to light up an LED. 
The DC servo comes with an [H-bridge](https://en.wikipedia.org/wiki/H-bridge) to control position 
and power in the DC motor. The servo also may need gears (gearbox) to increase output torque. All of it comes in a small and usually affordable package!

Hopefully, you bought SG92(R) servo. It's a small servo that offers a decent torque in a small casing. 
There are three wire leads: brown, red, orange. Colors may vary in tinge. The middle one, the
red one is a positive power supply. You'll connect 5V there. The brown one is GND. The orange one
is PWM signal, which controls the position of the servo. Make sure you connect it to PB1 pin.
The pinout of the servo is pretty smart. 5V lead in the middle effectively prevents you from applying
wrong polarity. If you connect the PWM lead to GND by mistake, nothing will happen! Of course, try
always to connect your hardware correctly.

| Servo  | Arduino Nano | Atmega Pinout |
|---|---|---|
| Orange | D9 | PB1 |
| Red | 5V | N/A |
| Brown  | GND | N/A |

There are many tutorials in the Web. You can google them or simply use one of the below links:
* [Arduino - Basic servo control](https://docs.arduino.cc/tutorials/generic/basic-servo-control/)
* [Adafruit - Servo tutorial](https://learn.adafruit.com/adafruit-arduino-lesson-14-servo-motors/overview)
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

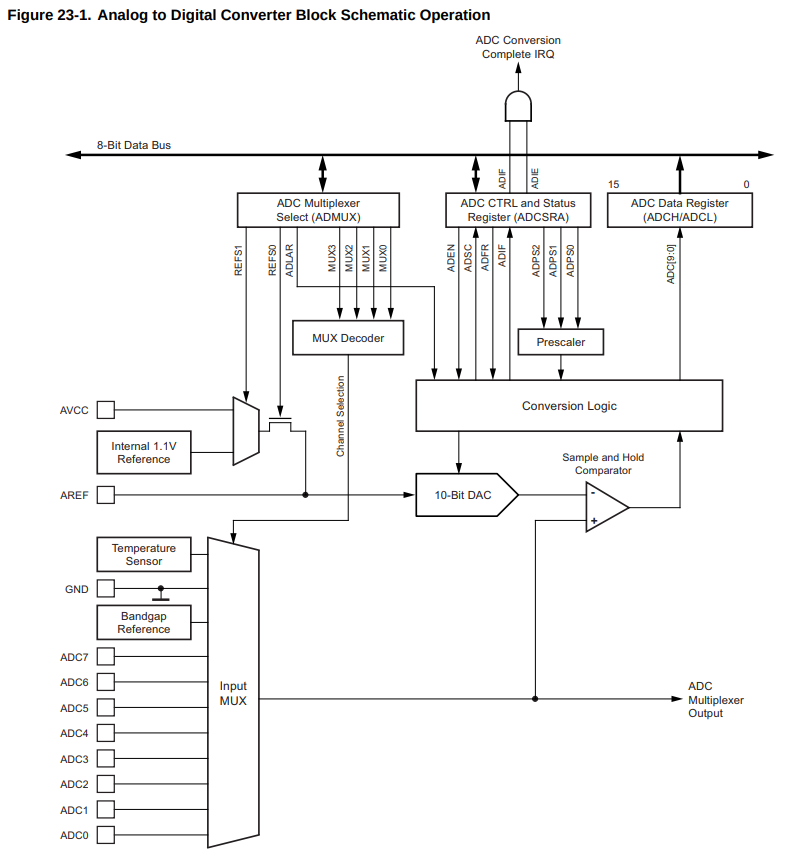
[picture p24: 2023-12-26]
docs/chapters/assets/images/chapter_2/1_adc_block_schematic.png

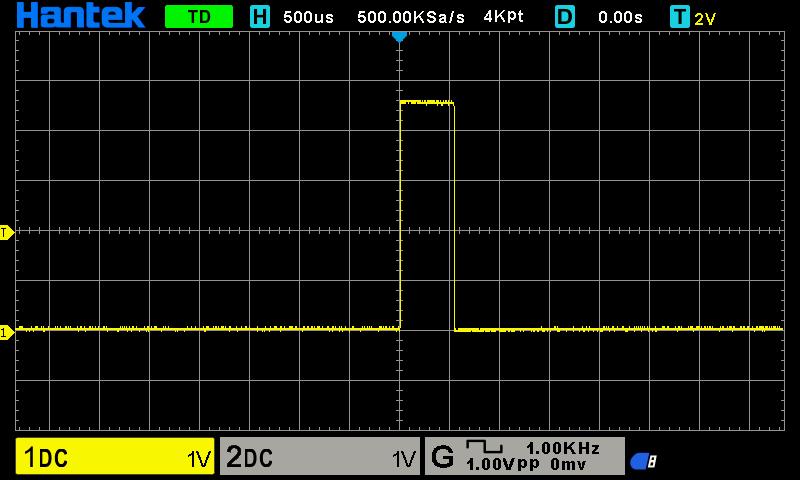
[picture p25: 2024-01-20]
docs/chapters/assets/images/chapter_5/02_servo_0deg_zoomin.jpg

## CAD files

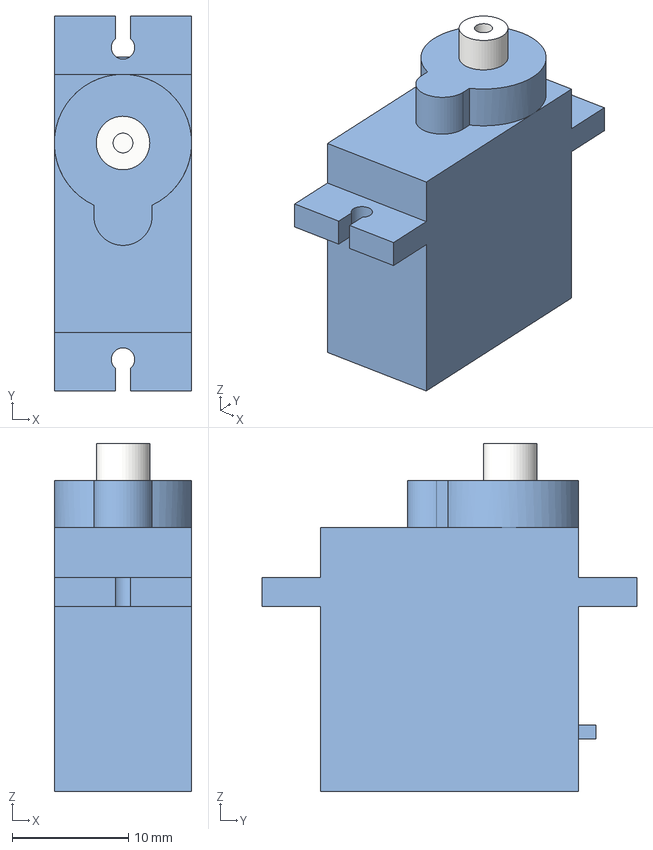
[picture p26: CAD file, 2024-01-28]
3d_models/SolidEdge/SG90_v7.step
11.8 x 32.2 x 29.9 mm

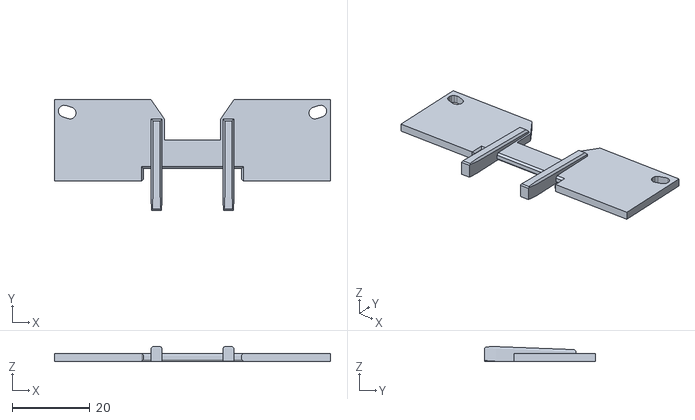
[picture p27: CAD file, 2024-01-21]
3d_models/stl/rear_wall.stl
71.0 x 28.6 x 3.77

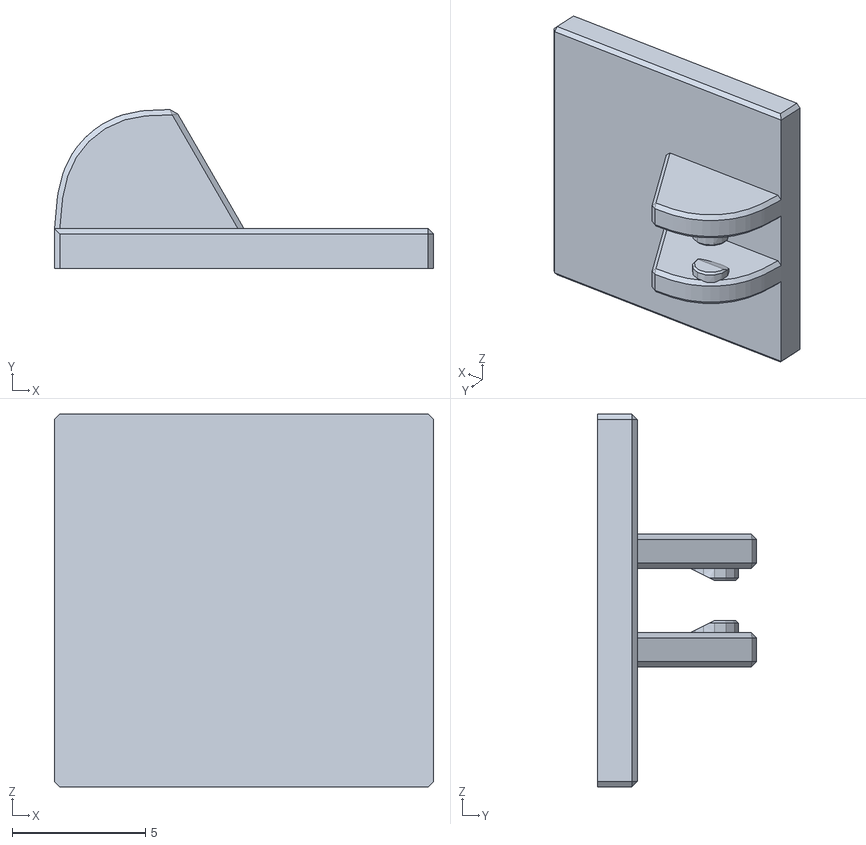
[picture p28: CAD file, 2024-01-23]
3d_models/SolidEdge/servo_arm_effector.stl
14.2 x 5.97 x 14.0

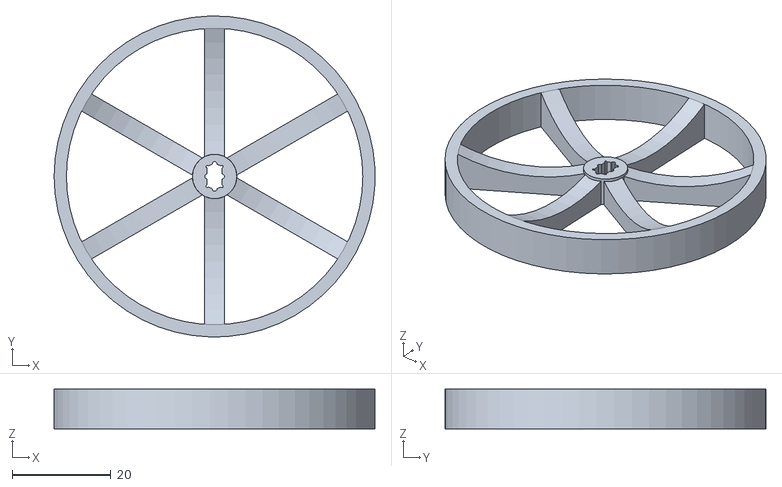
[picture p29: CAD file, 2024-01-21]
3d_models/stl/wheel.stl
65.0 x 65.0 x 8.00

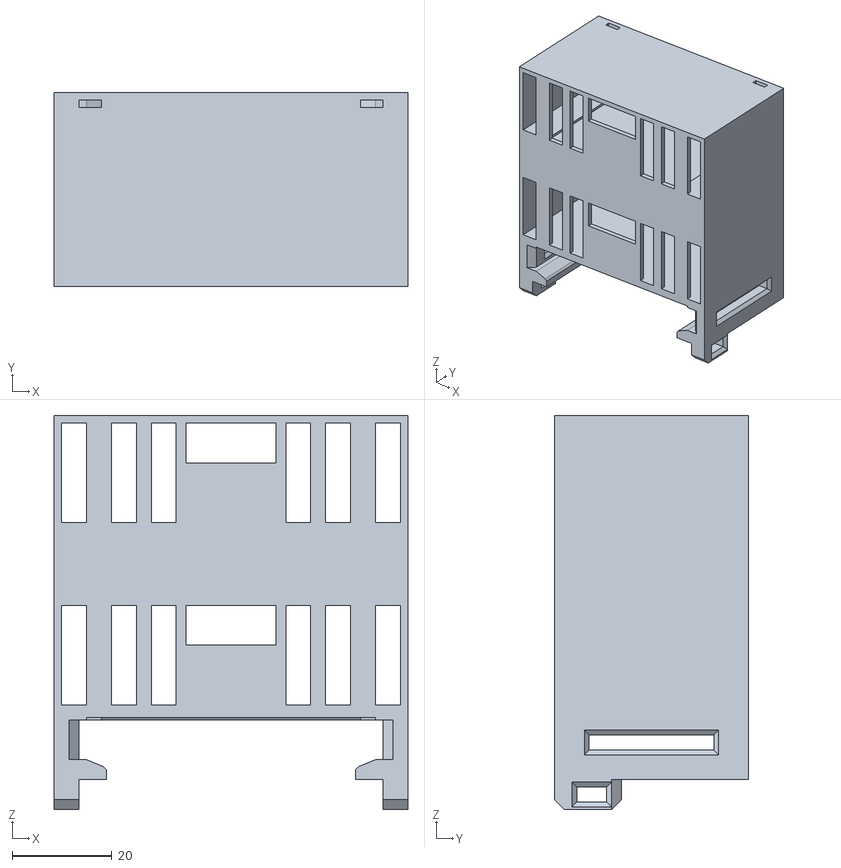
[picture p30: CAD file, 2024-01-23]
3d_models/SolidEdge/driver_tower_with_servo.stl
71.0 x 39.0 x 79.1

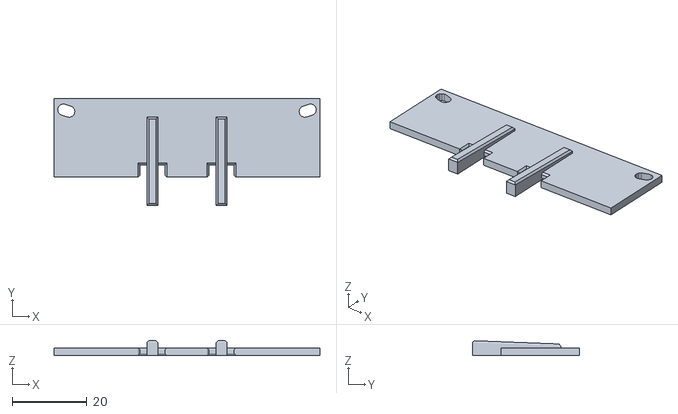
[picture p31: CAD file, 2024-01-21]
3d_models/stl/front_wall.stl
71.0 x 28.6 x 3.88

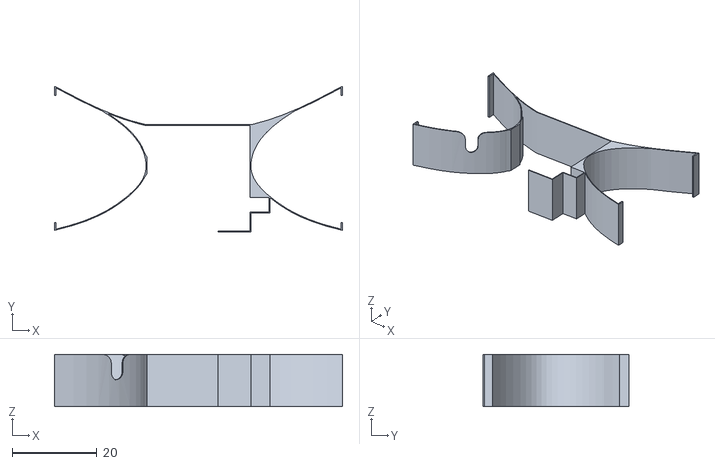
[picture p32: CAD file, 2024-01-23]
3d_models/SolidEdge/servo_holder.stl
68.0 x 34.4 x 12.3

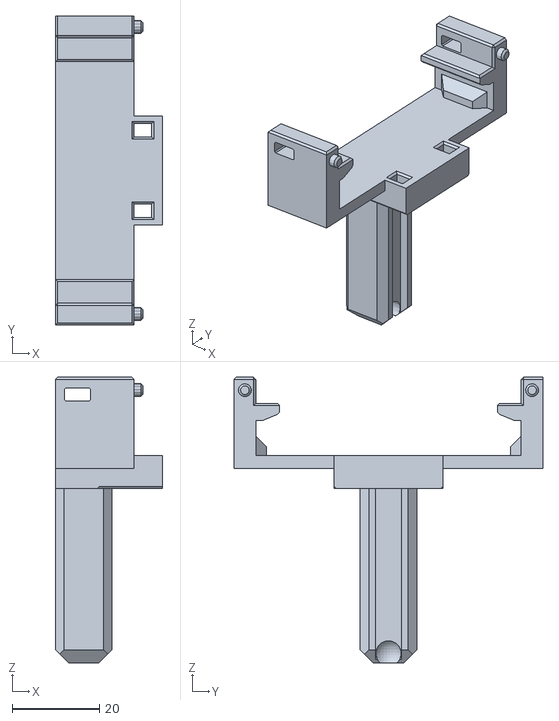
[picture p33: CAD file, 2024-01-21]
3d_models/stl/chassis_rear_beam_with_airsoft_bearing.stl
24.6 x 71.0 x 65.6

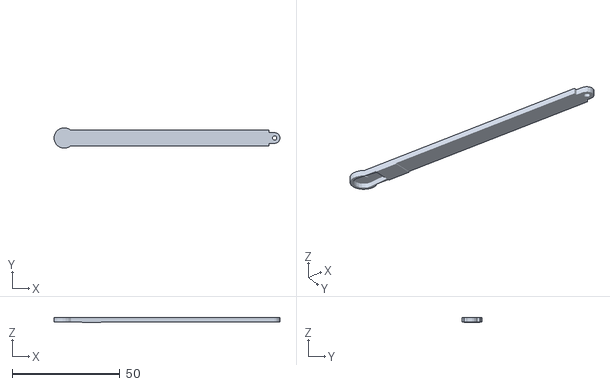
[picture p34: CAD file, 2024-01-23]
3d_models/SolidEdge/servo_arm.stl
104.7 x 9.42 x 2.30

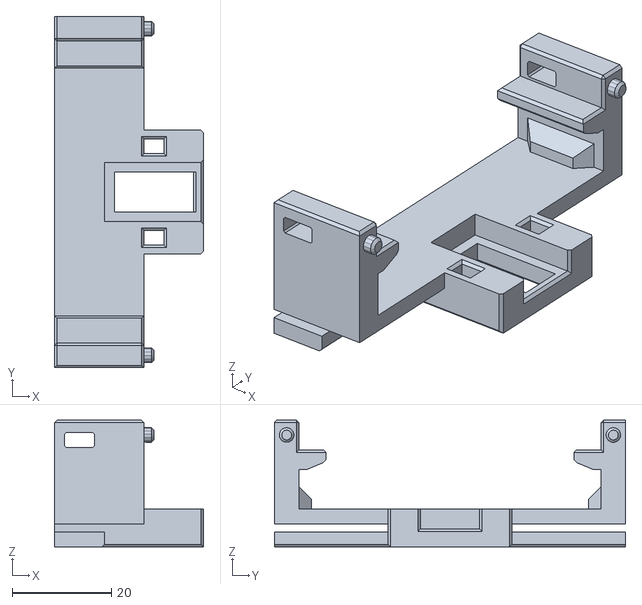
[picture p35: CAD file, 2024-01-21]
3d_models/stl/chassis_front_beam.stl
30.1 x 71.0 x 25.6

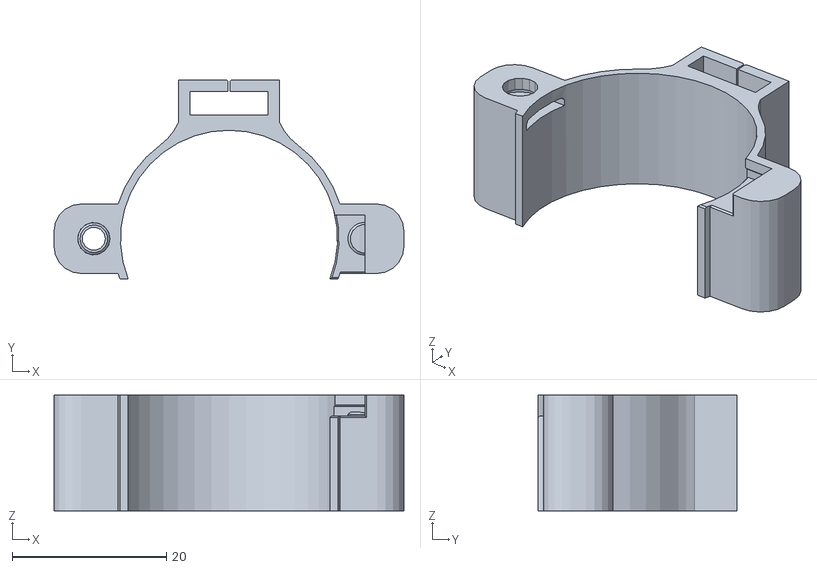
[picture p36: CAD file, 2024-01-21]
3d_models/stl/stepper_motor_case.stl
45.3 x 25.8 x 15.0

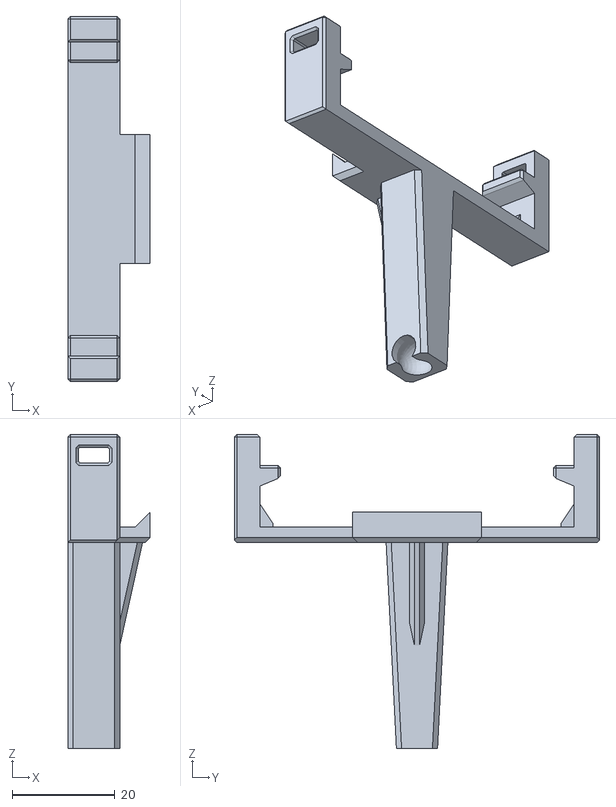
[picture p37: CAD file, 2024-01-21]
3d_models/SolidEdge/belka_podwozia_kulka.stl
16.0 x 71.0 x 61.0

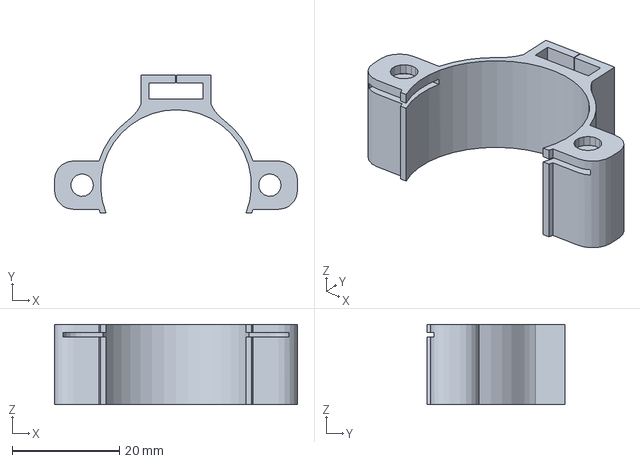
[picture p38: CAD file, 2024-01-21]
3d_models/SolidEdge/uchwyt-krokowiec.3mf
45.3 x 25.8 x 15.0 mm

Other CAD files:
3d_models/SolidEdge/uchwyt-krokowiec.stl

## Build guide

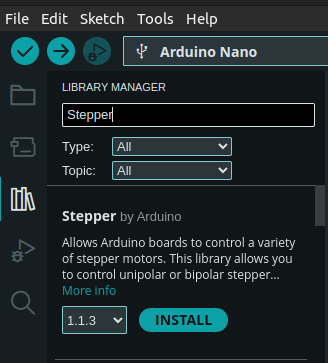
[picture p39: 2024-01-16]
docs/chapters/assets/images/chapter_4/1_stepper_library_install.png

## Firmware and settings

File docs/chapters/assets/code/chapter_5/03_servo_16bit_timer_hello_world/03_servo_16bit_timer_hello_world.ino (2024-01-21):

class Servo {
  public: 
  enum class SERVO_SELECTOR {
    SERVO_1,
    SERVO_2
  };
  static inline void setAngle(SERVO_SELECTOR servo, uint8_t angle) {
    uint16_t dutyCycle = map(angle, 0, 180, 540, 2540);

    switch (servo) {
      case SERVO_SELECTOR::SERVO_1:
        OCR1A = dutyCycle;
        break;
      case SERVO_SELECTOR::SERVO_2:
        OCR1B = dutyCycle;      // unused: COM1B1 is disabled
        break;
      default:
        break; 
    }
  }
};
void setup() {
  DDRB |= (1<<PB1); // Set PB1 as output
  /*
      Enable PWM on PIN PB1/Arduin D9

      CPU CLK, fclk_I/O = 16,000,000
      Timer: Phase Correct PWM, see 15.9.4 Phase Correct PWM Mode in Datasheet
      Formula: fOCnxPCPWM = fclk_I/O / {2* N * TOP}
      fOCnxPCPWM=50Hz
      Prescaler: N=8
      TOP = fclk_I/O / {2 * N * fOCnxPCPWM}

      TOP=ICR1=20000
  */
  TCCR1A = (1<<COM1A1)   // PB1 as PWM, see the pinout
      | (1<<WGM11);      // phase correct PWM, TOP=ICR1
  TCCR1B = (1 << WGM13) 
      | (1 << CS11);     // prescaler 8
  ICR1 = 20000;          // 50Hz 
}

void loop() {
  for (uint8_t angle = 0; angle <= 180; angle += 45) {
    Servo::setAngle(Servo::SERVO_SELECTOR::SERVO_1, angle);
    delay(1000);
  }
}

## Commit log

2023-12-12 Complete PIN output
2023-12-12 Add pullup resistor diagram
2023-12-17 Add Input AVR/Arduino tutorial part
2023-12-18 Add Interrupts section
2023-12-26 Start writing about ADC
2024-01-08 Add ADC section
2024-01-09 Add PWM section
2024-01-10 Add UART theory
2024-01-14 Add Arduino Serial read/write code examples
2024-01-15 Add Stepper motor docs
2024-01-16 Add library-based control of stepper motors, including some interrupts
2024-01-17 Add Servo theory
2024-01-20 Add Servo lib text
2024-01-21 Complete Servo chapter
2024-01-23 Add assembly pics
    [driver_tower_with_servo.stl, servo_arm.stl, servo_arm_effector.stl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]
2024-01-23 Add some printing tips
2024-01-25 Complete assembly steps
2024-01-27 Add missing item into BOM
2024-01-28 Add final pics
    [28BYJ-48_v5.cfg, 28BYJ-48_v6.stl, SG90_v7.step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]
2024-02-04 Fix some domain mistakes, typos and grammar
    [1_incremental_blink.ino, 3_pullup_and_software_debouncing.ino]
